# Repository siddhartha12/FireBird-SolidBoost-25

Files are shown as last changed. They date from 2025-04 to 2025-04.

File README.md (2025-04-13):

# FireBird-SolidBoost-25
# Background:
My design for Solid-Boost (Solid Rocketry Competition) held at Indian Institute of Technology - Banaras Hindu University (IIT-BHU) as part of their TechNex Tech festival

## Requirements for the design:
* Below 1kg
* F class motor (Upto 80N-s of thrust)
* 500m max apogee
* < 30m radius landing
# Design
## Structure
Fully 3d printed

## Propulsion
This rocket  designed to be used with simple KNO3 (Potassium Nitrate) + C12H22O12 (Sugar) in 65:35 ratio.

## Electronics
### Brains:
* Uses teensy 4.1 for sensor fusion and kalman filtering for maximum certainty
* write telemetry to a flash storage module
* Sends telemetry to an Arduino nano to write there for redundancy in telemetry at different frequencies for analysis

### Sensors:
* MPU9250 - for Inertial navigation + Gyroscope for orientation + Magentometer for earth orientation & positioning for waypoints guidance
* NEO-7M GPS - 

## Control
Uses a multiple phase approach:
* Powered Ascent - TVC gimbal (Pitch + Yaw) + Fins (Roll)
* Unpowered Ascent - Fins (Pitch, Yaw and Roll)
* Powered descent - Same as above
* Airbrake - Fins maximize AoA for slowing down
* deploy parachute at 30m

# Advantages:
* Very high controllability
* Very precise

# Disadvantages:
* Very complex code
* Is not a full working concept, needs a lot of iteration
* Better to start over on another one
* Too much 3d printing, more machines components would make it better
* Structural strength is absolute shite, not really airworthy
* Definitely a great learning experience

# Future improvements
* Actually implement a full Kalman filter for all states
* Use quaternions instead of Euler angles
* Make PCB for electronics (minimize weight)
* Implement forward control surfaces
* Make a larger motor
* Stick a camera on it
* Make a gimbal-able nozzle for the motor

# Outcome
* We were placed 2nd in the competition, beaten by a team of our own institution.

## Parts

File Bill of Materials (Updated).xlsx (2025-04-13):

 |  |  |  |  |  | 9001
Category wise cost
Avionics | 6995
Structural | 1484
Propulsion | 432
Part Name | Price per unit | Units needed | Total | Source | Link
Avionics
Teensy 4.1 | 2639 | 1 | 2639 | Robu | https://robu.in/product/buy-teensy-4-1-development-board/
MPU9250 | 430 | 3 | 1290 | Robu | https://robu.in/product/mpu9250-9-axis-attitude-gyro-accelerator-magnetometer-sensor-module-2/?gad_source=1
BMP280 | 30 | 2 | 60 | Robu | https://robu.in/product/bmp280-barometric-pressure-and-altitude-sensor-i2c-spi-module/
NEO 7M GPS | 548 | 1 | 548 | Robu | https://robu.in/product/neo-7m-000-neo-7m-gps-module-mwc-gy-neo-7m-v2-flight-control-gps-module-eeprom-mwc-apm2-5/
IRF520 MOSFET | 37 | 3 | 111 | Robu | https://robu.in/product/irf520-mosfet-driver-module-arduino-arm-raspberry-pi/
Arduino Nano | 195 | 1 | 195 | Robu | https://robu.in/product/arduino-nano-board-r3-with-ch340-chip-wo-usb-cable-solderedarduino-nano-r3-wo-usb-cable-soldered/
LM2596S Buck Coverter | 39 | 3 | 117 | Robu | https://robu.in/product/lm2596s-dc-dc-buck-converter-power-supply/
W25Q128 Flash Storage | 143 | 2 | 286 | Robu | https://robu.in/product/w25q128-large-capacity-flash-storage-module/
2S 1000mAh | 899 | 1 | 899 | Robu | https://robu.in/product/orange-1000mah-2s-20c-7-4v-lithium-polymer-battery-pack-lipo-2/
RM065 | 12 | 6 | 72 | Robu | https://robu.in/product/rm065-50350k-bochenchengdu-guosheng-tech-%C2%B125-100mw-50k%CF%89-plugin-potentiometers-variable-resistors-rohs/
SG90 Servos | 50 | 10 | 500 | Offline
Header Pins (10F + 10M) |  |  | 0 | Offline
Perfboard | 50 | 1 | 50 | Offline | https://robocraze.com/products/veroboard6x4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
4 core shielded cable | 54 | 2 | 108 | Robu | https://robu.in/product/24awg-multicore-insulated-cable4-cores-silicone/
electric match | 12 | 10 | 120 | IndiaMart | https://www.indiamart.com/proddetail/fireworks-ignitor-fuse-23950418191.html?
JST connectors (10F + 10M) | 90 | 1 | 90 | Robu | https://robu.in/product/3-pin-jst-xh-2-54mm-pitch-plug-and-socket-with-cable-10-pcs/
470uF capacitor (Teensy) |  | 2
1000µF electrolytic capacitor
1N5819 - Schottky Diode
10µF ceramic capacitors
0.1µF capacitor (3.3V-GND)
100Ohm Resistors |  | 20
7V TVS Diode SMBJ7.0
Battery Management system module
500mA PTC fuse
1A PTC fuse
330ohm (SPI)
10kohm resistor (pulldown for mosfet)
PESD5V0S1BA (ESD protection) | 4 |  |  | https://robu.in/product/pesd5v0s1ba115-nexperia-pesd5v0s1ba115-esd-protection-device-tvs-10-v-sod-323-2-pins-5-v/
Structural
M4 Threaded rods x 1m | 100 | 2 | 200 | OmRook | https://omrook.com/fasteners/bolts/threaded-rod/threaded-rod/
2mm Aluminium Plate 150x150 | 335 | 1 | 335 | amazn | https://www.amazon.in/Invento-Aluminium-Alloy-Sheet-150x150x2mm/
M4 nuts |  | 50 | 0 | Offline
ABS Filament (White) | 949 | 1 | 949 | Amazon
Propulsion
KNO3 (500g) | 432 | 1 | 432
Diodes
Power Source
SMBJ14A (Clamping Overvoltage)
Fast Blow 3.7A fuse (Overcurrent Protection) - at battery
SS54 (Reverse Current Protection)
Avionics Output
5.6V 1N5339B Zener Diode | Chandni
1A PTC Fuse - electronics
5A resettable fuse - servo
470uF Electrolytic Capacitor
1000uF Electrolytic Capacitor
2200uF Electrolytic Capacitor
10uF ceramic Capacitor
0.1uF ceramic capacitor
10kOhm
100Ohm

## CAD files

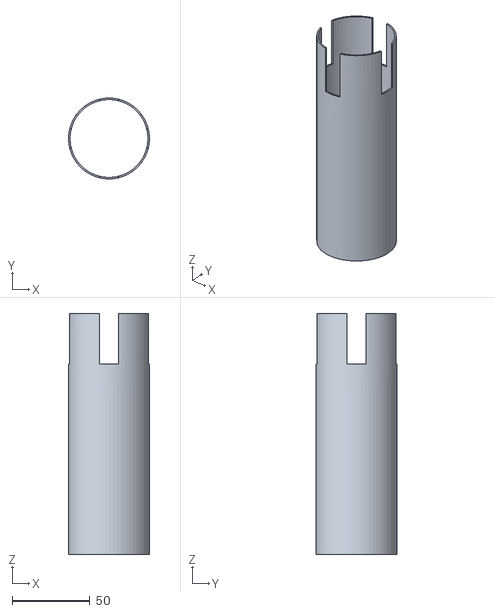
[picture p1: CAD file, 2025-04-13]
Print Files/Bottom Shell.stl
52.0 x 52.0 x 154.9

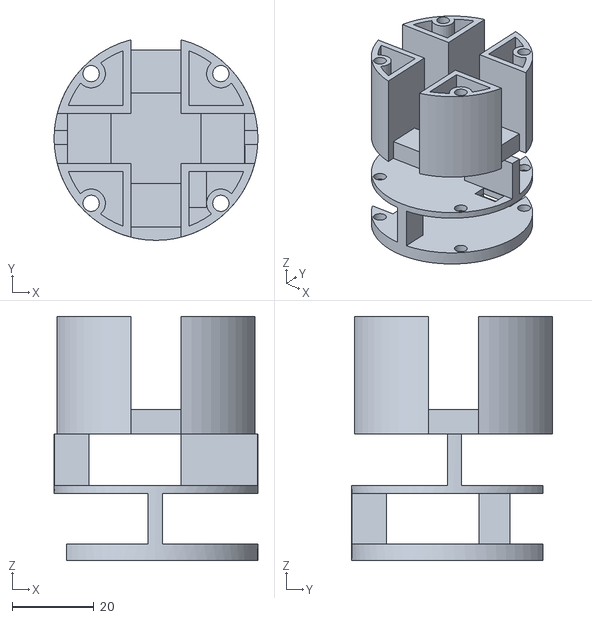
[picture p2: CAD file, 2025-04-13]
Print Files/Servo Enclosure housing.stl
50.0 x 49.2 x 59.9

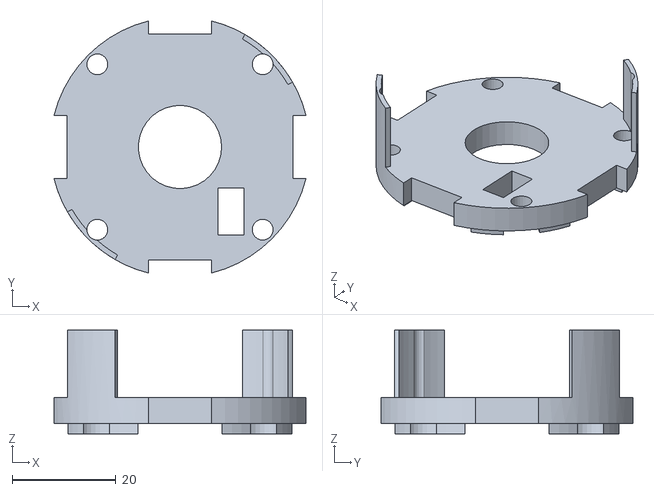
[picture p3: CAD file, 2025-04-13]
Print Files/Servo Enclosure Cap.stl
48.5 x 48.5 x 20.0

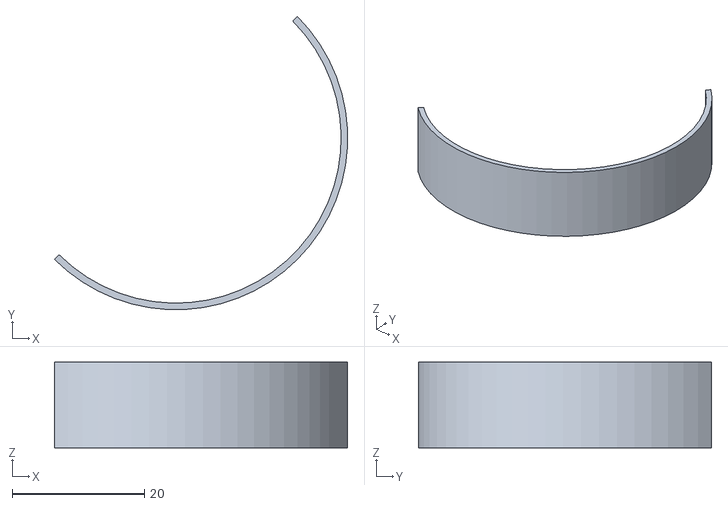
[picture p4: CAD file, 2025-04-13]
Print Files/Servo Enclosure Shell (2x needed).stl
44.3 x 44.3 x 13.0

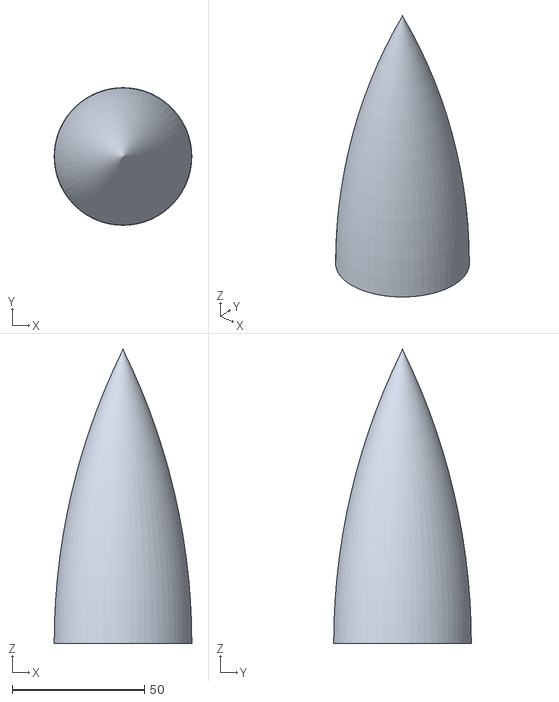
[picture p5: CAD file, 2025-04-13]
Print Files/Nose cone (outer).stl
52.0 x 52.0 x 111.0

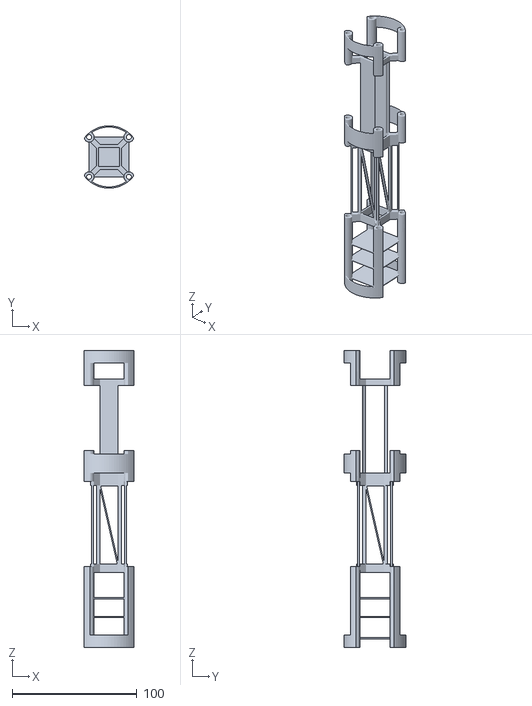
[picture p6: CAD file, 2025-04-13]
Print Files/Avionics Enclosure.stl
39.7 x 50.0 x 238.0

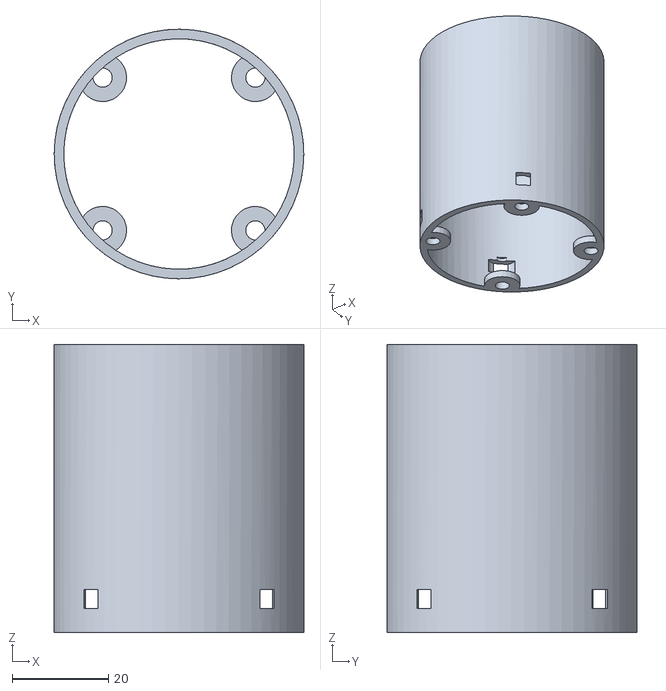
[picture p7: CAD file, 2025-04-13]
Print Files/Nose Cone (base).stl
52.0 x 52.0 x 60.0

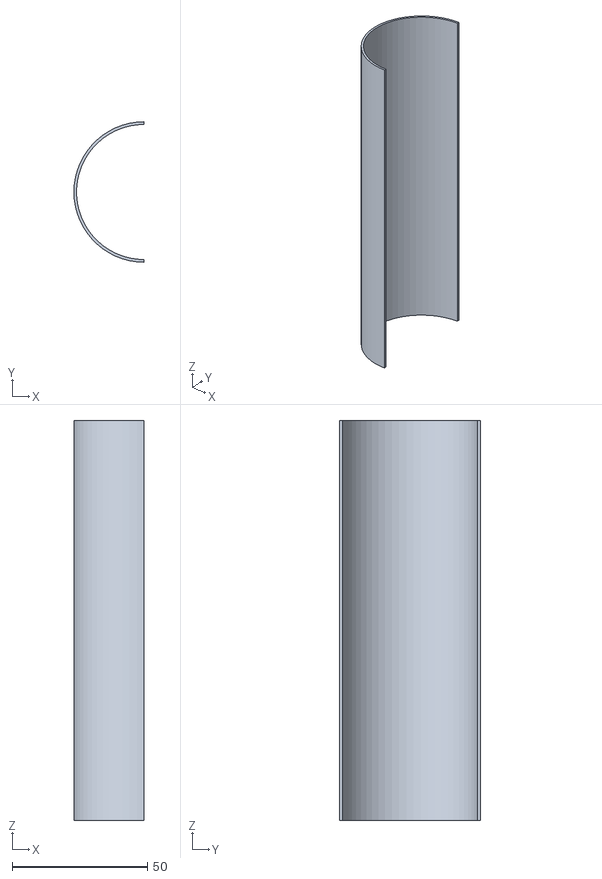
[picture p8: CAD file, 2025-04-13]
Print Files/Avionics shell (Outer, bottom, 2x needed).stl
26.0 x 52.0 x 148.0

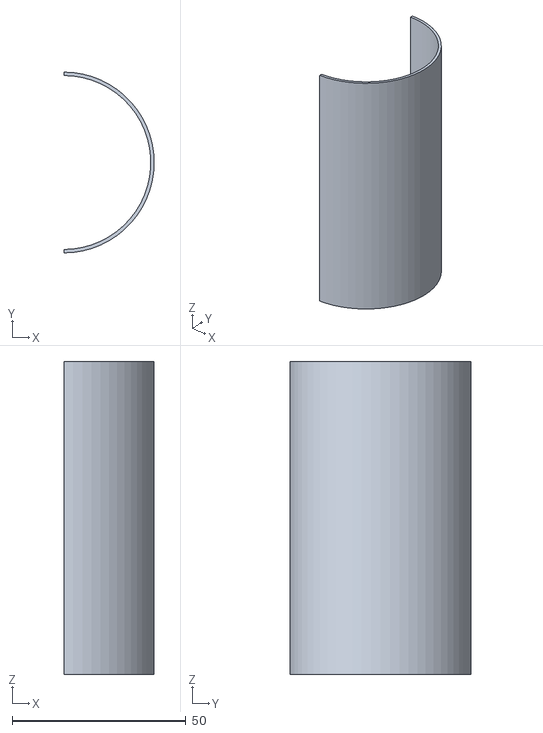
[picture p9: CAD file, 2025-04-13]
Print Files/Avionics Shell (Outer, upper, 2x needed).stl
26.0 x 52.0 x 90.0

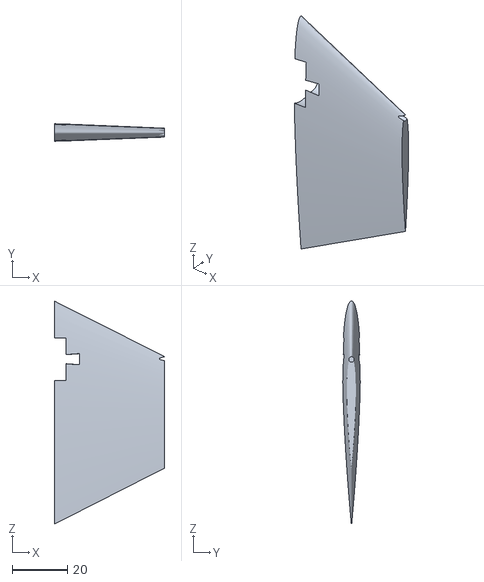
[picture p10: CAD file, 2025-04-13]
Print Files/Rocket Fin v11.stl
40.1 x 6.40 x 81.0

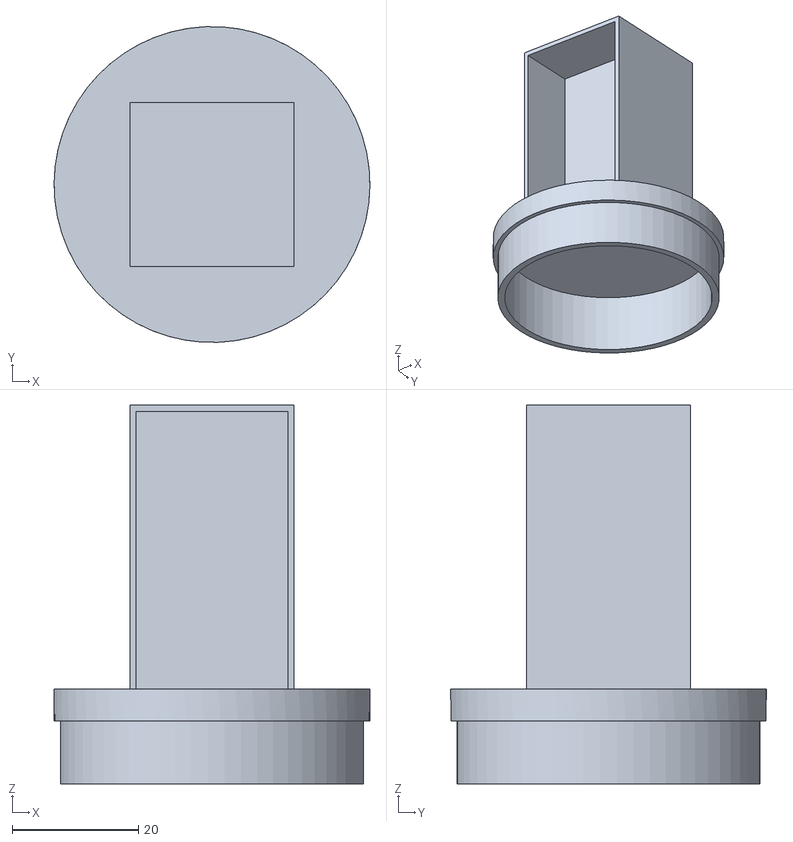
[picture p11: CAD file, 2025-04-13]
Print Files/Nose cone (Inner).stl
50.0 x 50.0 x 60.0

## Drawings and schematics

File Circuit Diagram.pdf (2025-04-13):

### TX0108E

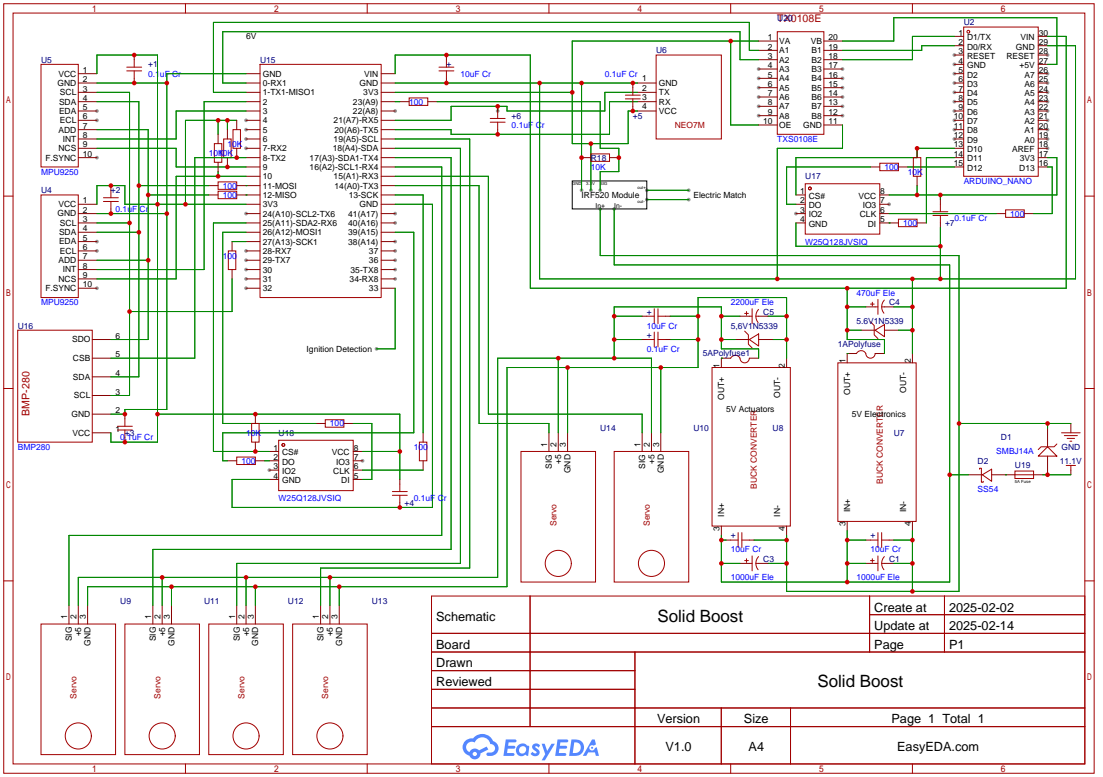
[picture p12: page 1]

Schematic | Solid Boost | Create at | 2025-02-02

Update at | 2025-02-14

Board | | Page | P1
Drawn | | Solid Boost
Reviewed

Version | Size | Page 1 Total 1
V1.0 | A4 | EasyEDA.com

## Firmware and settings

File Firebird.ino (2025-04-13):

#include <Wire.h>
#include <Adafruit_BMP280.h>
#include "MPU9250_asukiaaa.h"
#include <math.h>

struct Vector {
    float x, y, z;

    // Constructor
    Vector(float _x = 0, float _y = 0, float _z = 0) : x(_x), y(_y), z(_z) {}

    // Addition operator
    Vector operator+(const Vector& v) const {
        return Vector(x + v.x, y + v.y, z + v.z);
    }

    // Subtraction operator
    Vector operator-(const Vector& v) const {
        return Vector(x - v.x, y - v.y, z - v.z);
    }

    // Scalar multiplication
    Vector operator*(float scalar) const {
        return Vector(x * scalar, y * scalar, z * scalar);
    }

    Vector operator/(const Vector& v) const { 
      return Vector(x / v.x, y / v.y, z / v.z); 
    } // Element-wise division

    // Dot product
    float dot(const Vector& v) const {
        return x * v.x + y * v.y + z * v.z;
    }

    // Cross product
    Vector cross(const Vector& v) const {
        return Vector(
            y * v.z - z * v.y,
            z * v.x - x * v.z,
            x * v.y - y * v.x
        );
    }

    // Magnitude of the vector
    float magnitude() const {
        return sqrt(x * x + y * y + z * z);
    }

    // Normalize the vector
    Vector normalize() const {
        float mag = magnitude();
        return (mag > 0) ? (*this * (1.0 / mag)) : Vector(0, 0, 0);
    }

    // Print the vector
    void print() const {
        Serial.print("(");
        Serial.print(x);
        Serial.print(", ");
        Serial.print(y);
        Serial.print(", ");
        Serial.print(z);
        Serial.println(")");
    }
};

// Initializing sensors objects 
MPU9250_asukiaaa mpu1(0x68);  // MPU9250 #1 (AD0 tied to GND)
MPU9250_asukiaaa mpu2(0x69);  // MPU9250 #2 (AD0 tied to 3.3V)
Adafruit_BMP280 bmp;

//initialization variables
// 0 - Initialization
// 1 - Armed
// 2 - Powered Ascent
// 3 - Gliding
// 4 - Descent
// 5 - Airbrake
// 6 - Parachute Deployed
// 7 - Landed (All safe)
int status = 0;
float ParachuteHeight = 30.0;
float AirbrakeHeight = 80.0;

//Linear Movement Variables
Vector EulerPosition(0,0,0);
Vector EulerSpeed(0,0,0);
Vector RocketSpeed(0,0,0);
Vector EulerAcceleration(0,0,0);
Vector RocketAcceleration(0,0,0);

//angular terms
Vector GyroAcceleration(0,0,0);
Vector GyroSpeed(0,0,0);
Vector GyroOrientation(0,0,0);

//Navigation Terms
Vector InitialGPS(0,0,0);
unsigned long gps_ti;
unsigned long bmp_ti;

//guidance terms
Vector Correction(0,0,0);
int GuidanceMode = 0; //0 - Straight up/down; 1-Waypoint
int dt = 5;
static double theta_prev = 0.0;  // Retains value between calls
static double psi_prev = 0.0;    // Retains value between calls
float total_error_x = 0.0;
float total_error_y = 0.0;
float obs = 0.0;

// Waypoints for waypoint guidance mode
const int NUM_WAYPOINTS = 4;
Vector waypoints[NUM_WAYPOINTS] = {{0.0, 0.0, 100.0}, {10.0, 5.0, 200.0}, {0.0, 0.0, 300.0}, {0.0,0.0,80.0}};
int currentWaypoint = 0;
int DeployAirBrake = 0;

//other terms
float Apogee = 0;
int Error = 0;



void setup() {
    Serial.begin(115200);
}

void arm() {
  // put your setup code here, to run once:
  Wire.begin();  // Start I²C

  // Initialize MPU9250 #1
  mpu1.setWire(&Wire);
  mpu1.beginAccel();
  mpu1.beginGyro();
  Serial.println("MPU9250 #1 initialized");

  // Initialize MPU9250 #2
  mpu2.setWire(&Wire);
  mpu2.beginAccel();
  mpu2.beginGyro();
  Serial.println("MPU9250 #2 initialized");

  // Initialize BMP280
  if (!bmp.begin(0x76)) {  // Use 0x77 if SDO is tied to 3.3V
      Serial.println("BMP280 initialization failed! Check wiring.");
      while (1);
      Error += 1;
  }
  Serial.println("BMP280 initialized successfully!");
  //
  bmp.setSampling(Adafruit_BMP280::MODE_NORMAL,   // Continuous mode
                    Adafruit_BMP280::SAMPLING_X1,  // Temp oversampling x1
                    Adafruit_BMP280::SAMPLING_X1,  // Pressure oversampling x1
                    Adafruit_BMP280::FILTER_OFF,   // No IIR filter
                    Adafruit_BMP280::STANDBY_MS_1);  // Standby time 5ms (~100Hz)

  //Kalman Terms
  gps_ti = millis();
  bmp_ti = millis();
}

void loop() {
  // put your main code here, to run repeatedly:
  //Initialization
  while(status == 0){
    //communicate serially with the computer through GUI
    //write to major updates file with timestamp and position "INITIALIZED"
    if(){//arming sequence
      //write to major updates file with timestamp and position "ARMING SEQUENCE DETECTED"
      arm();
      if(){//do the self check of the rocket and if it returns true, ARM the rocket
        status = 1;
        //write to major updates file with timestamp and position "CHECKS DONE. ARMING SEQUENCE SUCCESSFUL."
      }
      else {
        //print out the possible error
      }
    }
  }
  //Armed
  while(status == 1) {
    //activate TVC
    KalmanUpdate(); //Updates positions
    ComputeGuidance();
    RollFins();
    TVCAdjust();
    WriteTelemetry();
    if(){//pin read high from launcher, or, detect certain acceleration for a certain time
      status = 2;
      //write to major updates file with timestamp and position "IGNITION DETECTED"
    }
    delay(dt); //5ms cycles 200Hz
    //write to Arduino
    //write to Flash to teensy
  }
  //Powered Launch
  while(status == 2) {
    //activate TVC
    KalmanUpdate(); //Updates positions
    ComputeGuidance();
    RollFins();
    TVCAdjust();
    WriteTelemetry();
    if(){// we detect that we are no longer accelerating
      status = 3;
      //write to major updates file with timestamp and position "BURNOUT DETECTED"
    }
    delay(dt);
  }
  //Gliding
  while(status == 3) {
    KalmanUpdate();
    ComputeGuidance();
    AdjustFins();
    WriteTelemetry();
    if(){//apogee detected (height max and current less) and velocity = 0
      status = 4;
      UpdateApogee();
      UpdateDescentWaypoint();
      //write to major updates file with timestamp and position "APOGEE DETECTED"
    }
    delay(dt);
  }
  //Descent
  while(status == 4) {
    KalmanUpdate();
    ComputeGuidance();
    AdjustFins();
    WriteTelemetry();
    if(DeployAirBrake == 1) {//at waypoint
      //Deploy Drag Brake
      status = 5;
      DeployAirbrake();
      UpdateParachuteHeight();
      //write to major updates file with timestamp and position "AIRBRAKE ACTIVATED"
    }
    delay(dt);
  }
  //Airbrake
  while(status == 5) {
    KalmanUpdate();
    WriteTelemetry();
    if(height == ParachuteHeight) {
      parachute_deploy();
      status = 6
      //write to major updates file with timestamp and position "PARACHUTE DEPLOYED"
    }
    delay(dt);
  }
}

Vector P[7] = { 
    Vector(1, 1, 1), Vector(1, 1, 1), Vector(1, 1, 1), 
    Vector(1, 1, 1), Vector(1, 1, 1), Vector(1, 1, 1), Vector(1, 1, 1)
};//covariance matrix for each state
Vector Q(0.01, 0.01, 0.01);  // Process noise
Vector R_GPS(5, 5, 5);       // Measurement noise for GPS
Vector R_IMU(0.1, 0.1, 0.1); // Measurement noise for IMU

void KalmanUpdate() {
  //Initialization
  
  //Prediction
  Vector EulerPositionPredict = EulerPosition + (EulerSpeed * dt) + (EulerAcceleration * (0.5 * dt * dt));
  Vector EulerSpeedPredict = EulerSpeed + (EulerAcceleration * dt);
  Vector RocketSpeedPredict = RocketSpeed + (RocketAcceleration *dt);

  Vector GyroOrientationPredict = GyroOrientation + (GyroSpeed * dt) + (GyroAcceleration * (0.5 * dt * dt));
  Vector GyroSpeedPredict = GyroSpeed + (GyroAcceleration * dt);


  //Getting sensor values
  // Averaging for 2xMPU
  // Euler(z) = MPU(X)
  // Euler(y) = MPU(Y)
  // Euler(x) = MPU(-Z)
  Vector mpu1acc(-(mpu1.accelZ()), mpu1.accelY(), mpu1.accelX());
  Vector mpu2acc(-(mpu2.accelZ()), mpu2.accelY(), mpu2.accelX());
  Vector mpuacc = (mpu1acc + mpu2acc) * 0.5;

  Vector mpu1gyro(-(mpu1.gyroZ()), mpu1.gyroY(), mpu1.gyroZ());
  Vector mpu2gyro(-(mpu2.gyroZ()), mpu2.gyroY(), mpu2.gyroZ());
  Vector mpugyro = (mpu1gyro + mpu2gyro) * 0.5;

  unsigned long gps_c = millis();
  unsigned long bmp_c = millis();
  if ((bmp_c - bmp_ti) >= 20) {
    float bmp_Altitude = bmp.readAltitude(1013.25);
    bmp_ti = bmp_c;
  }
  if ((gps_c - gps_ti) >= 100) {
    float gps_x;
    float gps_y;
    float gpsxdot = getGpsVelocities('x');
    float gpdydot = getGpsVelocities('y');
  }
  
  
  //Measure part:
  //Gyrospeed we will directly get from measurement (Apply complementary filter)
  //GyroOrientation we will get directly (Apply Complementary Filter)
  //Rocket Acceleration aajayegi (Complementary filter) - no need for sensor fusion
  //Rocket speeds we can get from that
  //Euler Acceleration we can convert from RocketAcceleration to Euler Frame
  //Euler Speeds and Positions from Acceleration
  //Measured part
  Vector GyroSpeedMeasured = mpugyro;
  Vector GyroOrientationMeasured; //complementary filter with IMU & Gyro

  Vector EulerPositionMeasured; // When GPS comes in (BMP every 50ms, Updates with BMP evry 2 cycles, Updates with GPS every 20 cycles)
  Vector EulerSpeedMeasured; // GPS comes in (BMP every 50ms, updates with BMP every 2 cycles, Updates with GPS every 20 cycles)
  Vector RocketSpeedMeasured; //Not measured. Only from IMU and reverse transformation of GPS speeds

  
}

void ComputeGuidance() {
    //initializing terms for guidance
    Vector Target;
    
    if (GuidanceMode == 0) {
        // Target is just the vertical trajectory
        Target.x = 0;
        Target.y = 0;
        Target.z = EulerPosition.z + 1; // Just ensure we always move upwards
    } 
    else if (GuidanceMode == 1) {
        // Target is the next waypoint
        /*x_target = waypoints[currentWaypoint].x;
        y_target = waypoints[currentWaypoint].y;
        z_target = waypoints[currentWaypoint].z;*/
        Vector Target = waypoints[currentWaypoint];

        // Check if we reached the waypoint
        float dist = (Target - EulerPosition).magnitude()
        if (dist < 5) { // 5m tolerance
            if (currentWaypoint >= NUM_WAYPOINTS - 1) {
                GuidanceMode = 0;
            }
            else {
              currentWaypoint++;
            }
            
        }
    }

    // Compute position error
    float error_x = EulerPosition.x - Target.x;
    float error_y = EulerPosition.y - Target.y;
    total_error_x += error_x;
    total_error_y += error_y;
    obs += 1.0;

    
    // Compute velocity direction to the target
    float theta_desired = atan2(EulerSpeed.x, EulerSpeed.z); // Pitch error
    float psi_desired = atan2(EulerSpeed.y, EulerSpeed.z);   // Yaw error

    // Compute rate of change of error
    float theta_error = theta_desired;
    float psi_error = psi_desired;
    
    float theta_dot = (theta_error - theta_prev) / (dt/1000);
    float psi_dot = (psi_error - psi_prev) / (dt/1000);

    theta_prev = theta_error;
    psi_prev = psi_error;

    // Proportional Navigation Law (Corrective acceleration)
    float N = 3.0; // Gain for guidance
    Correction.x = -N * theta_dot * EulerSpeed.z - error_x;
    Correction.y = -N * psi_dot * EulerSpeed.z - error_y;
    Correction.z = 0; // No correction in vertical
}

void UpdateDescentWaypoint() {
  float wind_x = (total_error_x/obs) * 0.6;//avg error per m in xe due to wind
  float wind_y = (total_error_y/obs) * 0.6;//avg error per m in ye due to wind
  float descent_distance = Apogee - AirbrakeHeight;
  //error racked up between that distance
  float x_compensation = -0.9 * (descent_distance * wind_x);
  float y_compensation = -0.9 * (descent_distance * wind_y);
  waypoints[3].x = x_compensation;
  waypoints[3].y = y_compensation;
  waypoints[3].z = AirbrakeHeight;
}

void DeployAirbrake() {
  //set all fins to 90
}
